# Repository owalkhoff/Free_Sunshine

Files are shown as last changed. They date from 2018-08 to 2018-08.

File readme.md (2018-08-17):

# Free Sunshine!

Promoting mechatronic art & sustainable energy in South Africa one g☼ggab☼t at a time

## What is this project about?

It is about spreading access to and an interest in electronics and art.

It also raises awareness about sustainable energy and the current development in South Africa of legislation regarding small scale solar energy generators. The project is driven by Miranda Moss and Oliver Walkhoff and is made possible with the support of the Swiss Arts Council Pro Helvetia. Find out more on the project website:

[freesunshine.org](http://freesunshine.org)

## What is a g☼ggab☼t?

A g☼ggab☼t is a small solar-powered robot. About 200 of them have been built in workshops during ISEA 2018, Durban, and subsequently at Baleni Senior Secondary School, Kwazulu Natal, South Africa.

A g☼ggab☼t consists of a printed circuit board (pcb), one or two solar cells, a motor, a capacitor and some mechanical parts. For the workshops, the pcb was pre-populated with smd components. The participants soldered the larger components to the board and added bristles, wire, beads and other things to create their individual bot.

## How can I build my own g☼ggab☼t?

We have created a pamphlet with a short description of the parts and some building instructions:

[Pamphlet in English](pdf/goggabot_pamphlet_english.pdf)

[Pamphlet in Zulu](pdf/goggabot_pamphlet_zulu.pdf)

## How does the circuit work?

A schematic and a short description of the g☼ggab☼t circuit is also on the pamphlet. It was contributed by Uwe Schüler of Kulturgüter-Schuppen, Dusslingen, Germany.

[www.kulturgueter-schuppen.de](http://www.kulturgueter-schuppen.de)

## How was the pcb made?

The pcb was created using KiCad Version 4.0.7. The boards were manufactured by PCBWay in China, and assembled by R2 Manufacturing, Glattbrugg, Switzerland.

The KiCad and Gerber files which were used for production can be found [in this repository](goggabot).

This is a rendering of the front, with components:

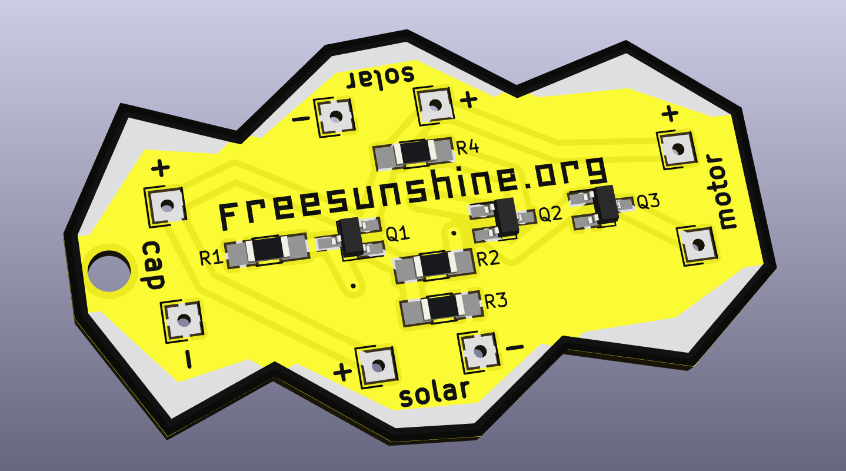
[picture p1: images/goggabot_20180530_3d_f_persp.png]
pcb front


And here is the back:

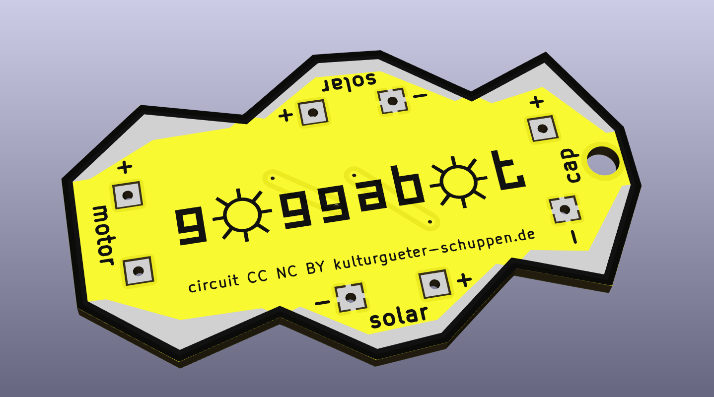
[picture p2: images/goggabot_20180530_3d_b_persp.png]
pcb back


## License

The g☼ggab☼t circuit is CC NC BY kulturgueter-schuppen.de.

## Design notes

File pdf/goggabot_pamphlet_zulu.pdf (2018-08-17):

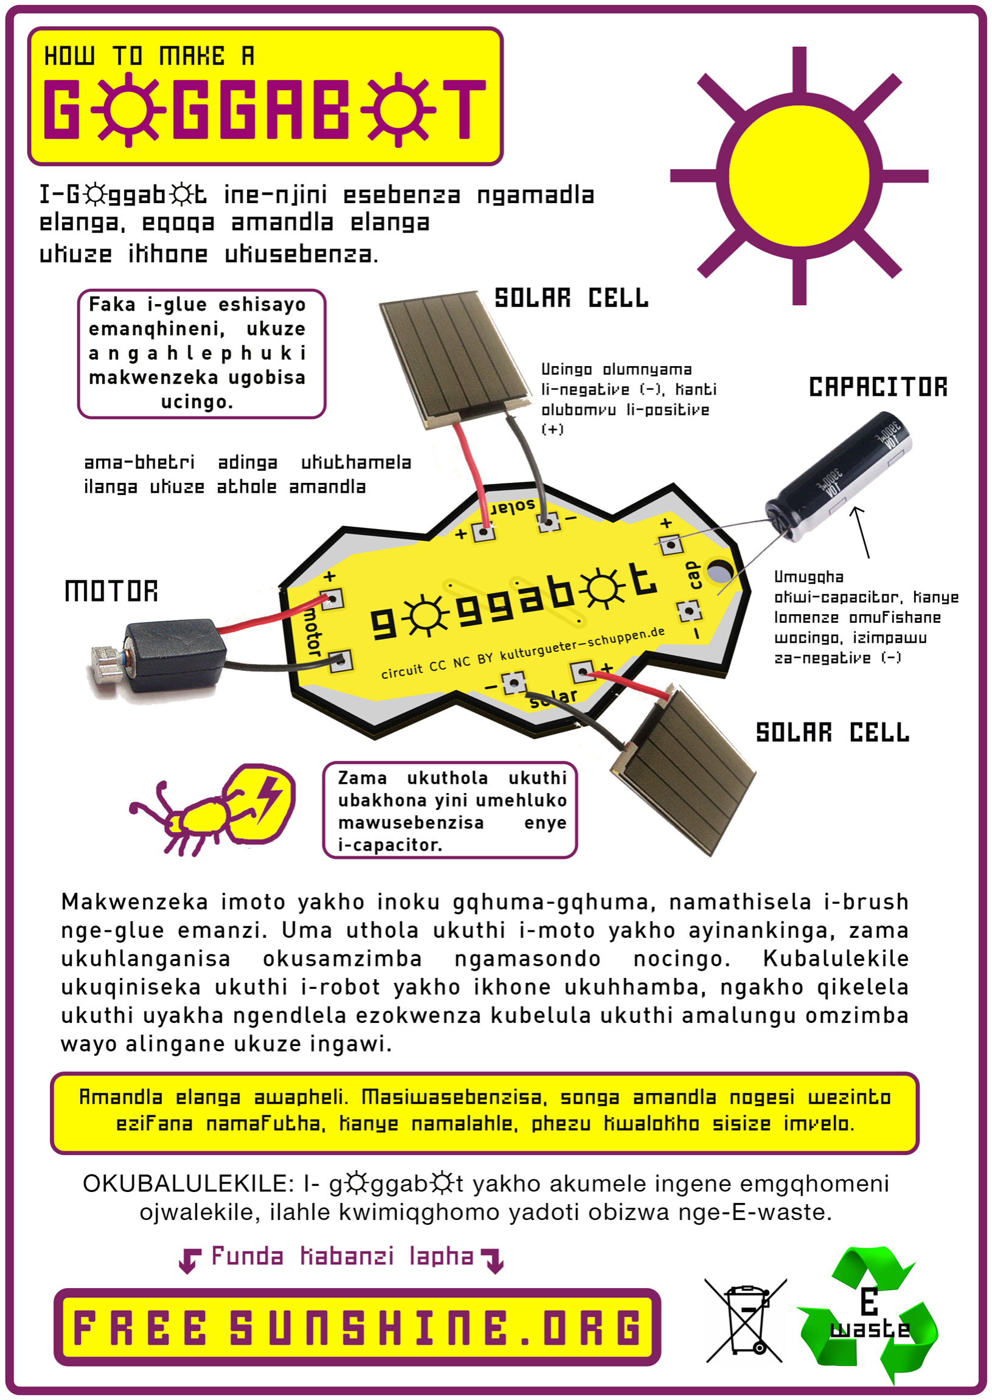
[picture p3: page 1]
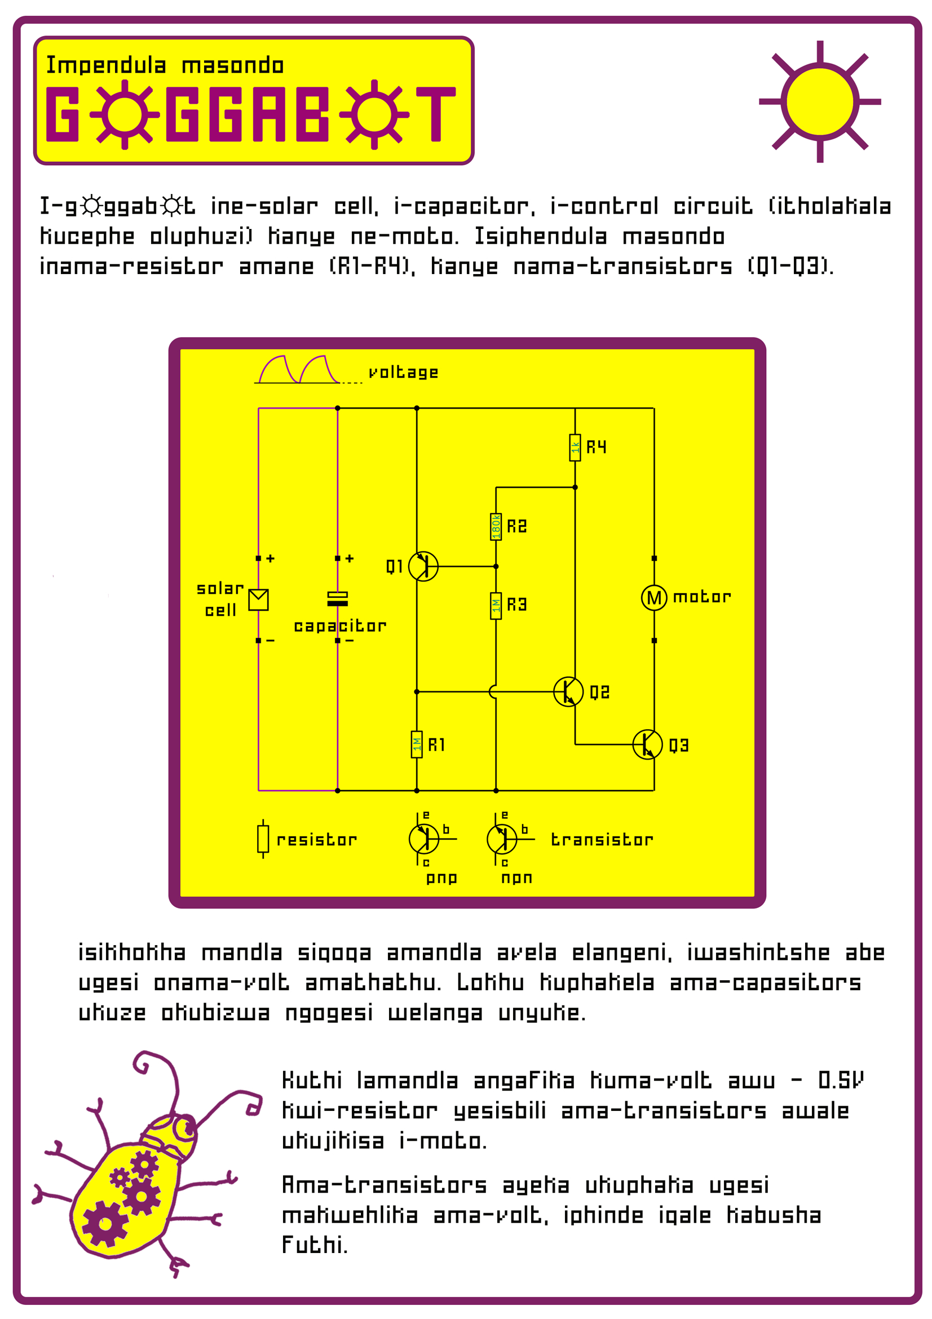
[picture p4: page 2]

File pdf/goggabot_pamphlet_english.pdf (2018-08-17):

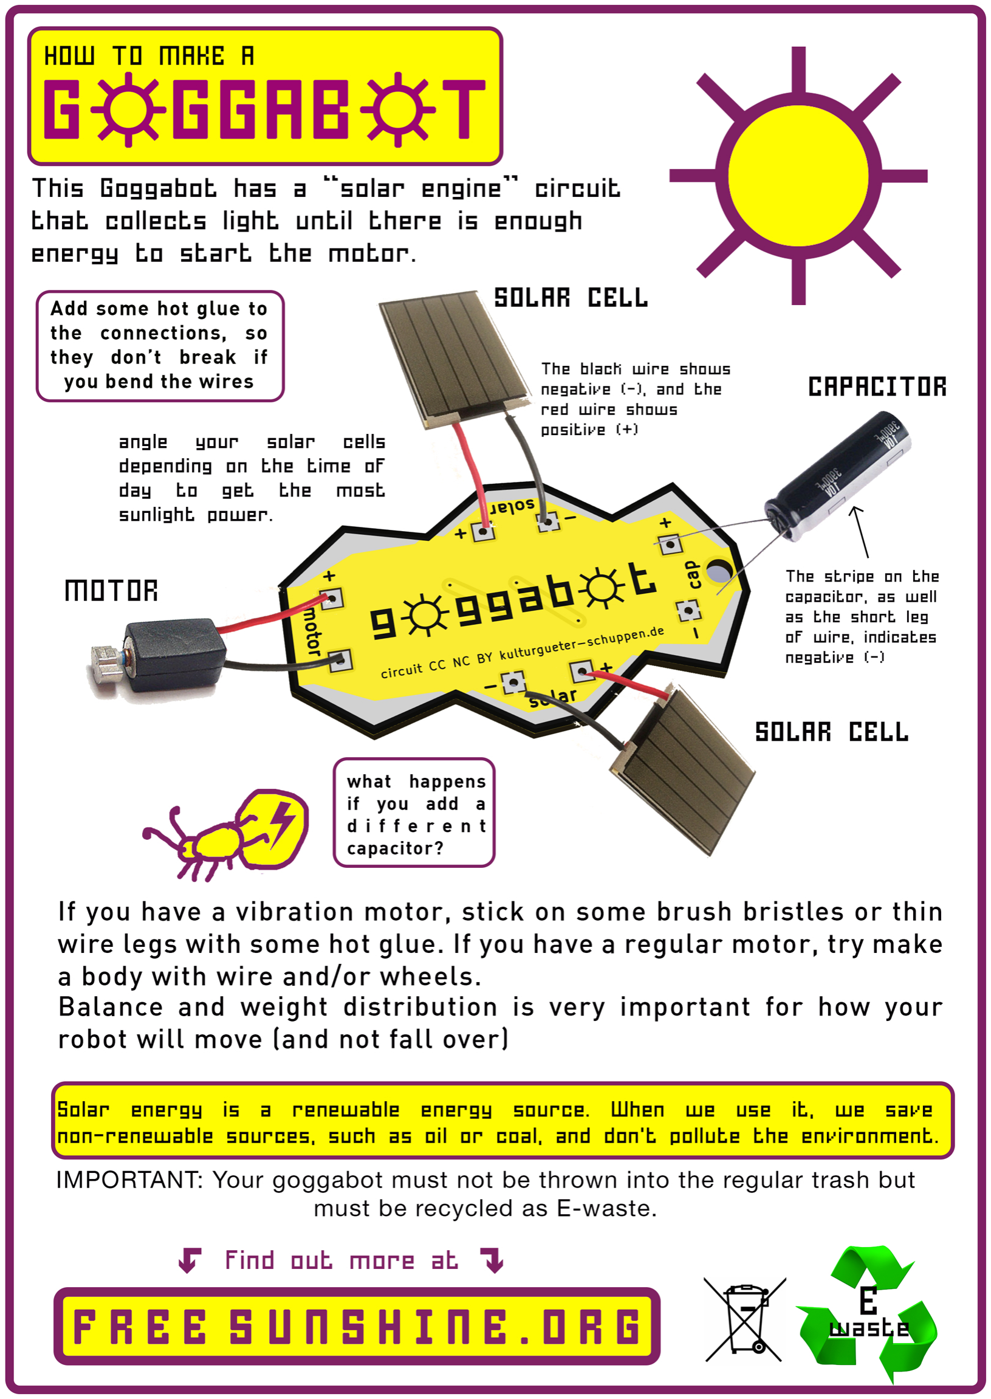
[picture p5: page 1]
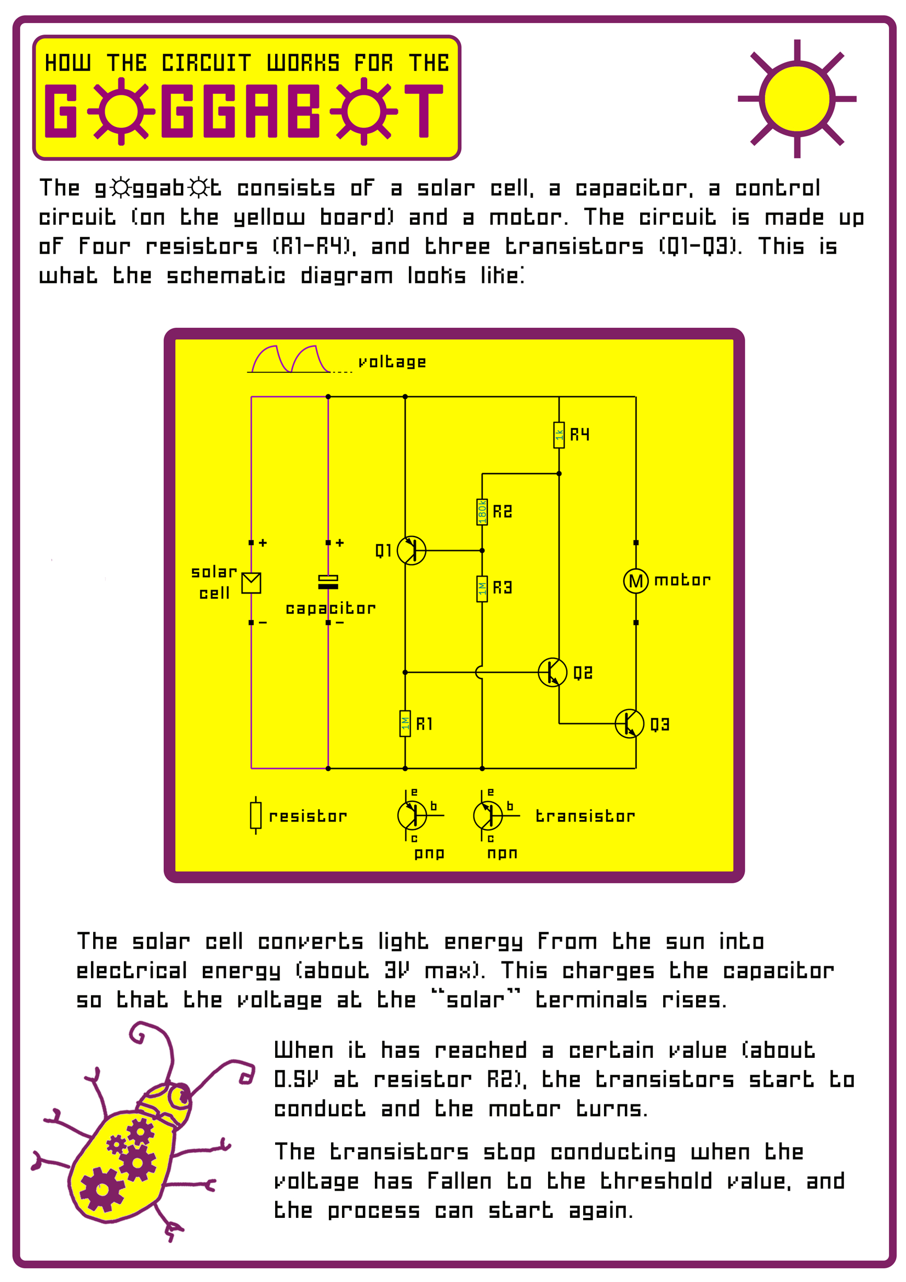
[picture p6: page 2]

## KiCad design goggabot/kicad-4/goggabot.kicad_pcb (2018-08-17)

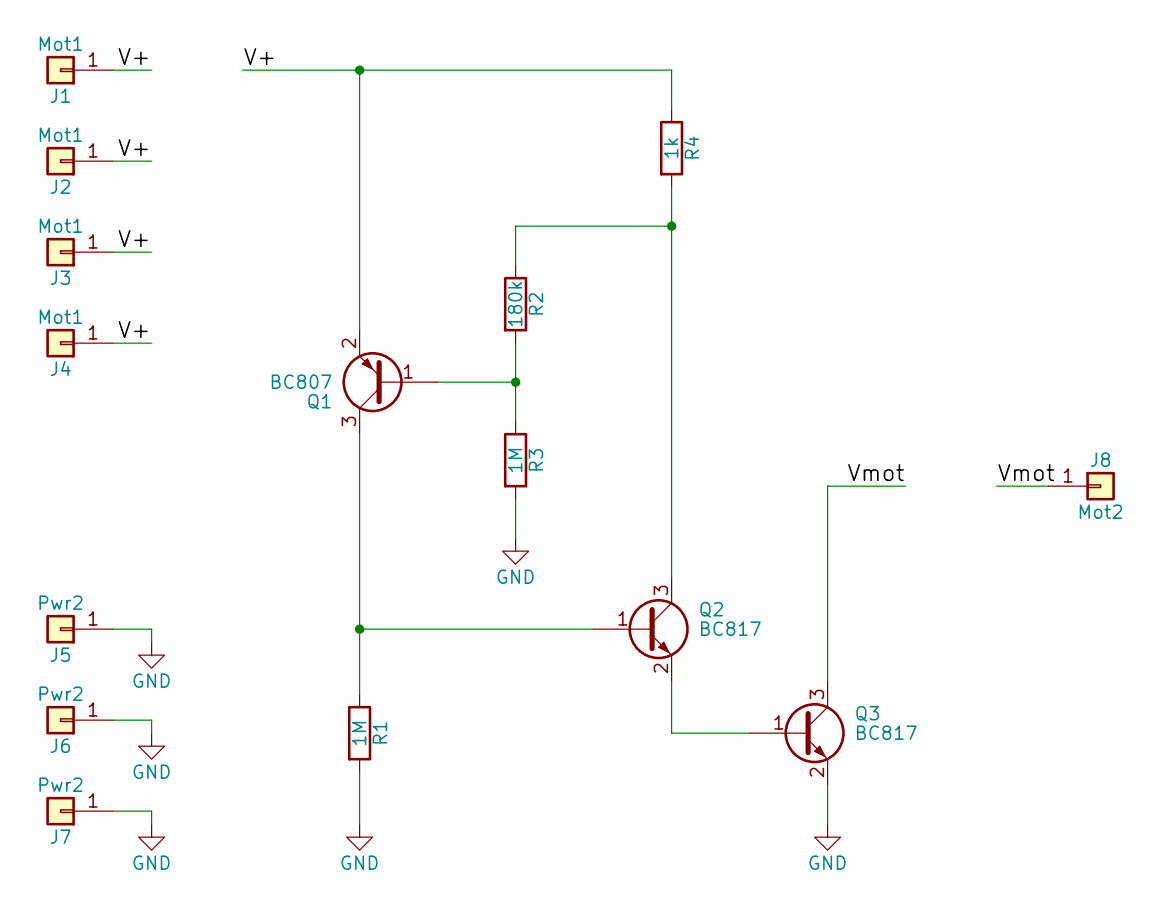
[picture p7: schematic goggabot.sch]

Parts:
J1, J2, J3, J4: Mot1; Socket_Strip_Straight_1x01
J5, J6, J7: Pwr2; Socket_Strip_Straight_1x01
J8: Mot2; Socket_Strip_Straight_1x01
Q1: BC807; SOT-23
Q2, Q3: BC817; SOT-23
R1, R3: 1M; R_1206_HandSoldering
R2: 180k; R_1206_HandSoldering
R4: 1k; R_1206_HandSoldering

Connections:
/V+: J1.1, J2.1, J3.1, J4.1, Q1.2 (E), R4.1
/Vmot: J8.1, Q3.3 (C)
GND: J5.1, J6.1, J7.1, Q3.2 (E), R1.2, R3.2
unnamed: Q1.1 (B), R2.2, R3.1
unnamed: Q1.3 (C), Q2.1 (B), R1.1
unnamed: Q2.2 (E), Q3.1 (B)
unnamed: Q2.3 (C), R2.1, R4.2

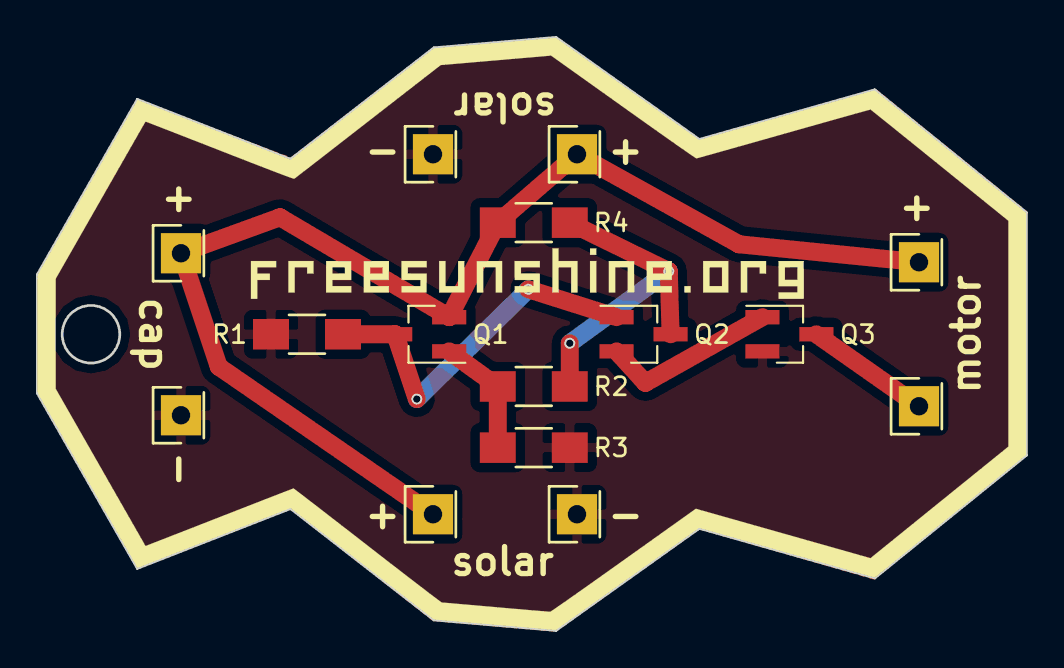
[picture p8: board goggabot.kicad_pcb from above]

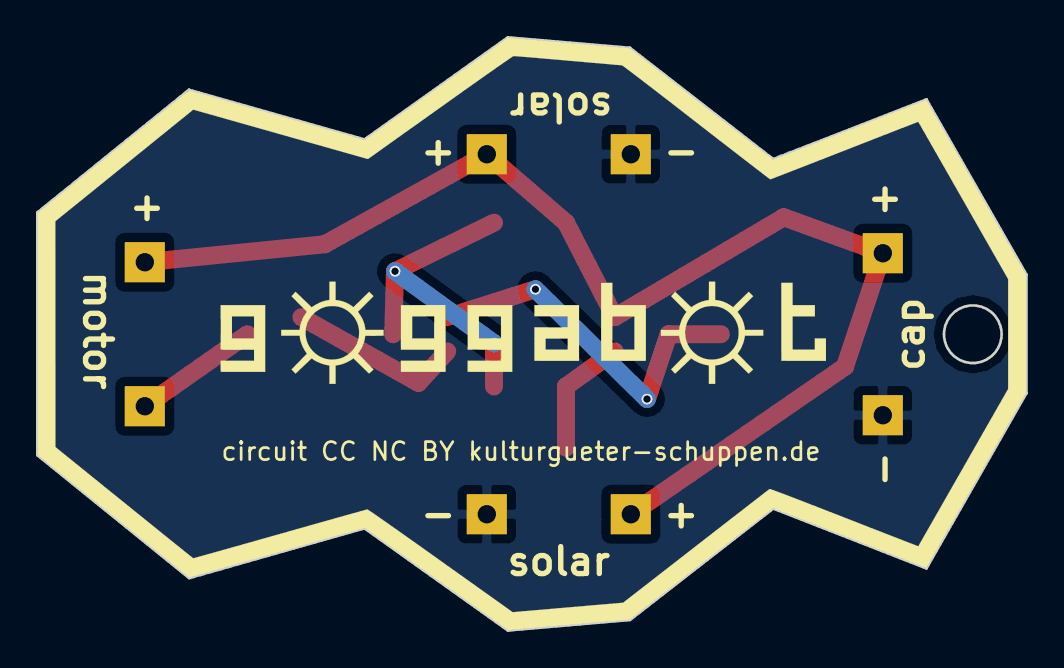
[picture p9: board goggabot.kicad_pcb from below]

Board: 2 copper layers, 55.0 x 33.0 mm, 21 parts (3 on the bottom side), 7 nets.

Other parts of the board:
freesunshine: LOGO; goggabot_freesunshine_31x3
goggabot: LOGO; goggabot_logo_34x6
mask: LOGO; goggabot_55x33_mask
mask#2: LOGO; goggabot_55x33_mask
outline: LOGO; goggabot_55x33_outline_1mm
outline#2: LOGO; goggabot_55x33_outline_1mm

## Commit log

2018-08-17 Add KiCad and Gerber files
    These were used for production. Made with KiCad 4.0.7.
    [goggabot-B.Cu.gbr, goggabot-B.Mask.gbr, goggabot-B.SilkS.gbr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]
2018-08-17 Add BOM
    [BOM.csv]
